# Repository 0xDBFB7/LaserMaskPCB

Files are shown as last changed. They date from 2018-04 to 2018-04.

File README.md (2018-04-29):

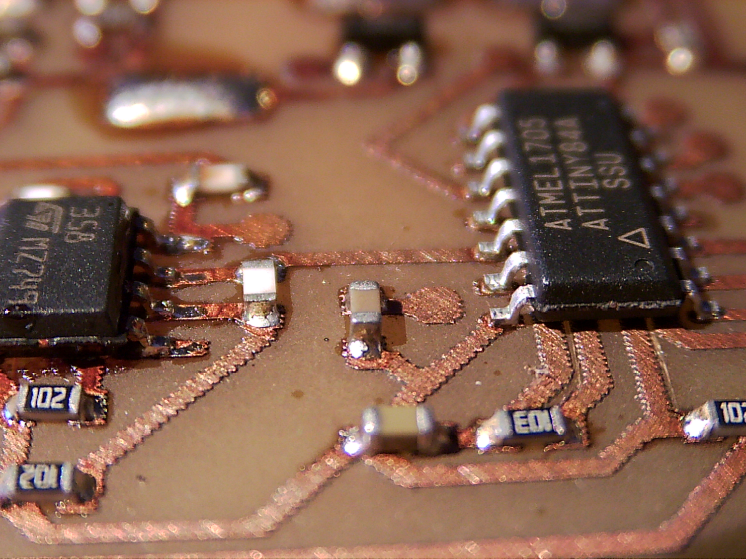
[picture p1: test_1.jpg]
Test 1

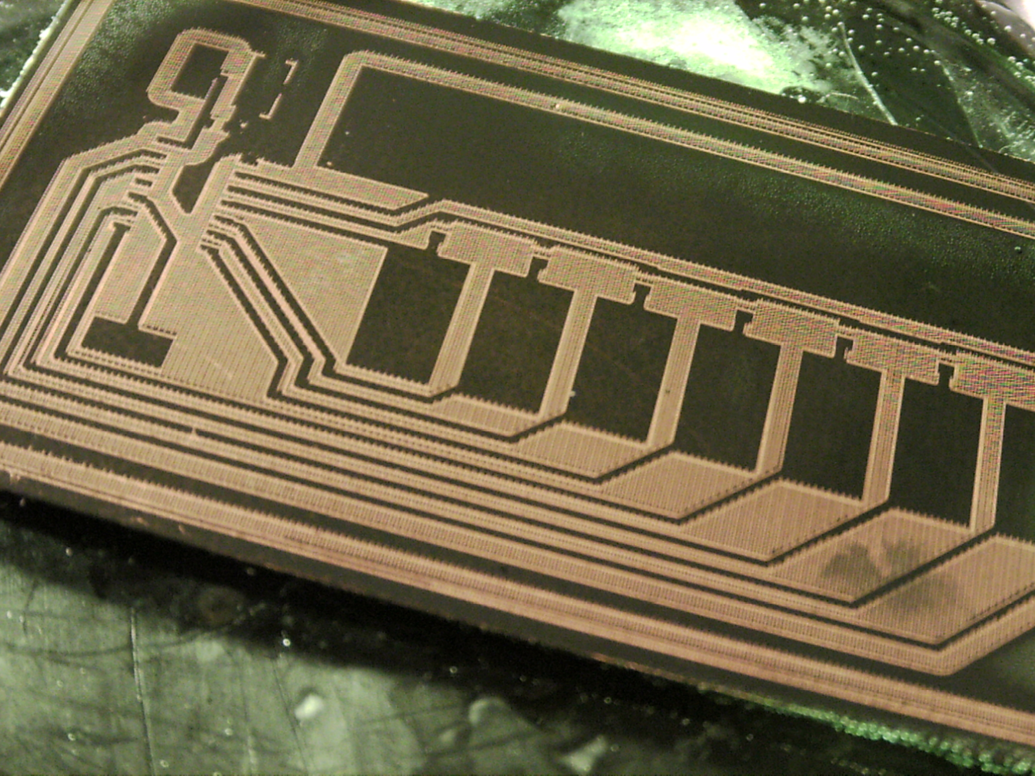
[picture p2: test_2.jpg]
Test 2


### Some background

After watching [this video](https://www.youtube.com/watch?v=1hFNj86L7sk) from Marco Reps on using an Eleksmaker A3 laser cutter with a paint mask technique for PCB manufacturing, I figured I'd try to set up a system for prototype production.

This led me down a rabbit hole that ended with me getting sprayed in the face by a jet of chlorine gas and hydrochloric acid.

#### But why

###### boards are so cheap these days, just order them in

In my style of R&D (that is, "be disorganized and fail every time at everything"), the rate at which you can iterate designs seems to be essential. After each board revision, you gather more data and characterize your design slightly more - and any lag between new information and new hardware seems to impede the process significantly. This lag component only be an issue for me, though - someone more competent may have other predictors for success.

Over the last few years, I've tried off-and-on to etch my own boards - however, all the techniques I'd tried had serious repeatability issues. 

We generally use a local PCB supplier for our prototype boards, meaning that our hardware lag is about 3 days.

With the laser cutter, we were able to build a complete, populated PCB in under 3 hours.

It still isn't worth it.

#### Code

Like CNC trace milling, Marco produced his boards using a single, laser-width isolation, using a vector file of his board. Because of the small dot size of the laser cutter, I found this very difficult to solder, even with a reflow oven. I wanted something with a configurable isolation region.

This repo includes an Eagle CAM job for generating all the files required to build a double-sided board, a set of scripts for generating G-code for drilling, a set of bash scripts for processing the CAM generated files, and a LaserWeb4 workspace file that etches all the layers (and a paste stencil!).

To use, just:

	1. Buy a LaserWeb compatible laser
	2. Install ghostscript and inkscape on a Debian-like distro
	3. Run laser.cam on your board using Eagle.
	4. Copy over the generated files
	5. Run laser.sh
	6. Import the laserweb workspace
	7. Select the workspace layers
	9. Put a pre-masked board in your laser cutter [see below]
	8. Put on your goggles
	9. Laser!
	10. Etch the board in your choice of solution [see below]
	11. Cut the stencil on the laser
	12. Reflow
	13. Profit!

#### Process parameters

I have several pages of notes that I have yet to transfer into a human-readable form.

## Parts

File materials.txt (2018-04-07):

Matte paint on copper:

100mm - 0.2 - incomplete removal.
500mm - 0.1 - dot size has a big effect on the amount of residue that remains.
1000mm - 0.1 - when fully dried, you can brush the residue off.

Paint must be fully dried before etching - 70c for 20 minutes seems to do it.

White masking tape on copper:

500mm - dot size 0.1 - Traces gummed with adhesive.
800 - Same.
1200 - right out. Completely covered traces.

Kapton Polyimide on copper:

1000 "cuts" with a thick black trace - but does not cleanly go through.

Even 100/100 is unable to puncture reliably. Higher power densities appear 
to just cause a buildup of white material.

Dry film negative resist:

1500 - 100 - nice purple color, but it burned right through.
2000 - 40 - Works really well.
2000 - 30 - 0.08 Again, works really well. 

Three minutes in a tablespoon of washing soda developer seems to work.

20 seconds at "rayon" seems to fuse.

Buna-N rubber:

300 - 100 - 0.08 - not all the way through - pretty smokey.
100 - 100 - 0.08 - 2 passes - Still only a quarter of the way through.
100 - 100 - 0.08 - 7 passes - Only half way through.
20 - 100 = 0.08 - 2 passes - most of the way through, but the Buna changed
texture completely in a manner that I think makes it unsuitable for gaskets.

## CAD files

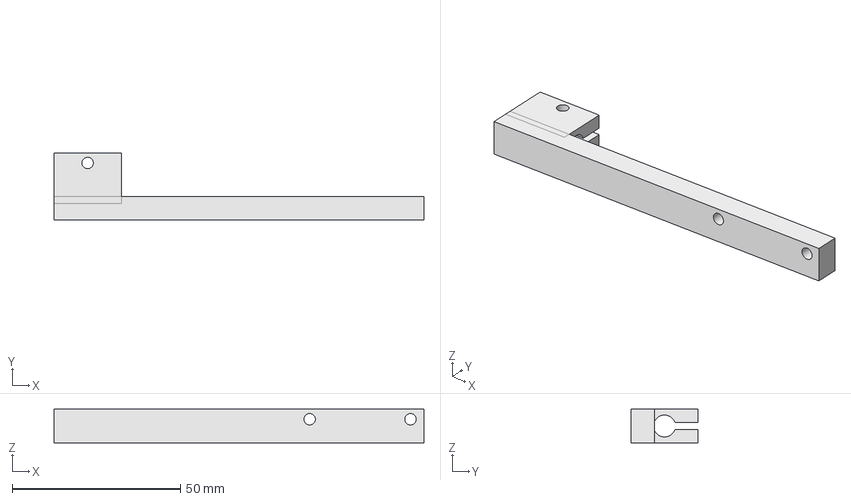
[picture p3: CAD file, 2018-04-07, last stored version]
A3_laser_mechanical/endoscope_mount.fcstd
110.0 x 20.0 x 10.0 mm

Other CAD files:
A3_laser_mechanical/endoscope_mount.stl

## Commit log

2018-04-03 First functional commit
    [endoscope_mount.fcstd, endoscope_mount.stl]
2018-04-07 Functional, added materials.txt
    [endoscope_mount.fcstd, endoscope_mount.stl]
2018-04-29 More descriptive readme
    [endoscope_mount.fcstd, endoscope_mount.stl]
